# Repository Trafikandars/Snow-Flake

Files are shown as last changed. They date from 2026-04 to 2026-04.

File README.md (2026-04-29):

# Snow-Flake
Machine à Neige DMX pour le Theâtre - DMX Snow Flake Machine for theater

Ce projet vous est proposé par la compagnie Trafikandars :

C'est une machine permettant de lâcher des cotillons ou autre, contrôlable en DMX.
La construction nécessite des pièces imprimées en 3D et un circuit imprimé sur mesure. 
Tous les fichiers sont disponibles ici pour que vous puissiez la faire vous-même. 
Si vous n’avez pas le matériel nous vous proposons de vous envoyer un kit contenant tous les éléments nécessaire à son assemblage pour la monter ou de vous l’envoyer prête à l’usage.
Si vous trouvez des pistes d'améliorations je reste ouvert à toute requet : Trafikandars.workshop@gmail.com

Conception 3D : Adem Koanda_Saurel

Code : Côme Douville

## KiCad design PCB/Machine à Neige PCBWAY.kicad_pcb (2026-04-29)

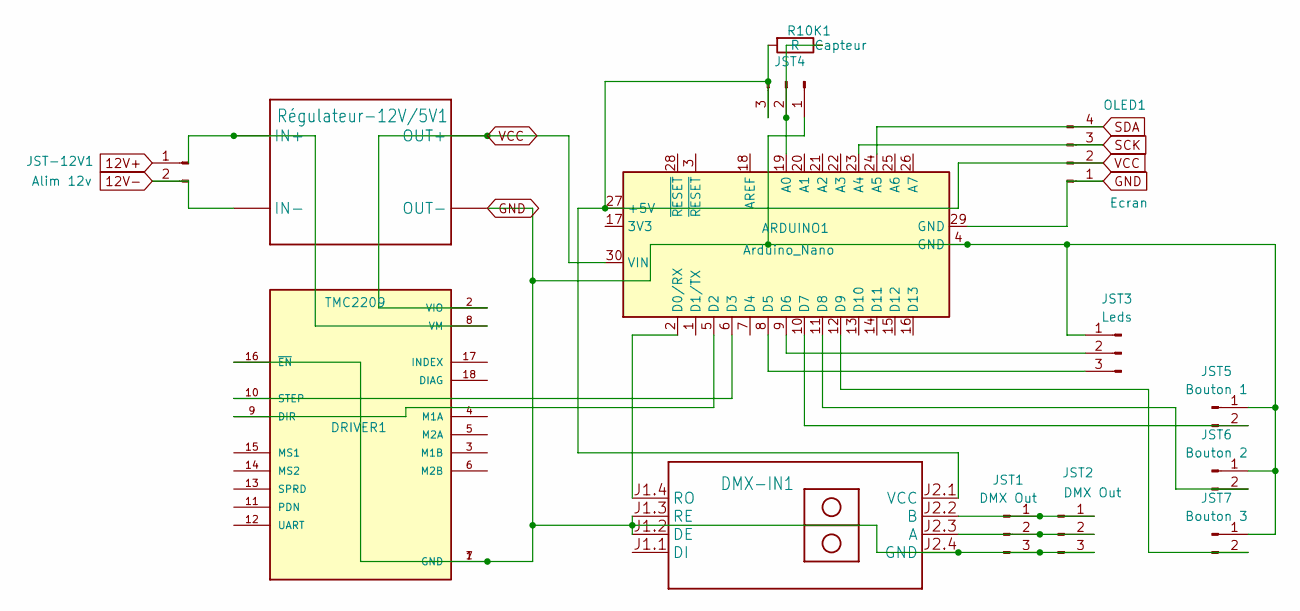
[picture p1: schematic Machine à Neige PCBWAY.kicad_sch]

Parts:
ARDUINO1: Arduino_Nano
DMX-IN1: RS485-TTL-CONVERTER
DRIVER1: TMC2209; MODULE_TMC2209_SILENTSTEPSTICK; PARTREV 1.20
JST1, JST2: DMX Out; PinSocket_1x03_P2.54mm_Vertical
JST3: Leds; PinSocket_1x03_P2.54mm_Vertical
JST4: Capteur; PinSocket_1x03_P2.54mm_Vertical
JST5: Bouton 1; PinSocket_1x02_P2.54mm_Vertical
JST6: Bouton 2; PinSocket_1x02_P2.54mm_Vertical
JST7: Bouton 3; PinSocket_1x02_P2.54mm_Vertical
JST-12V1: Alim 12v; PinSocket_1x02_P2.54mm_Vertical
OLED1: Ecran; PinSocket_1x04_P2.54mm_Vertical
R10K1: R; R_Axial_DIN0207_L6.3mm_D2.5mm_P5.08mm_Vertical
Régulateur-12V/5V1: StepDown-lm2596

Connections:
12V+: JST-12V1.1
12V-: JST-12V1.2, Régulateur-12V/5V1.2 (IN-)
GND: ARDUINO1.4 (GND), ARDUINO1.29 (GND), DMX-IN1.J1.2 (DE), DMX-IN1.J1.3 (RE), DMX-IN1.J2.4 (GND), DRIVER1.1 (GND), DRIVER1.7 (GND), DRIVER1.16 (~EN), JST1.3, JST2.3, JST3.1, JST4.1, JST5.1, JST6.1, JST7.1, OLED1.1, Régulateur-12V/5V1.4 (OUT-)
unnamed: ARDUINO1.19 (A0), JST4.2, R10K1.1
unnamed: ARDUINO1.2 (D0/RX), DMX-IN1.J1.4 (RO)
unnamed: ARDUINO1.5 (D2), DRIVER1.9 (DIR)
unnamed: ARDUINO1.6 (D3), DRIVER1.10 (STEP)
unnamed: ARDUINO1.8 (D5), JST3.3
unnamed: ARDUINO1.9 (D6), JST3.2
unnamed: ARDUINO1.10 (D7), JST5.2
unnamed: ARDUINO1.11 (D8), JST6.2
unnamed: ARDUINO1.12 (D9), JST7.2
unnamed: DMX-IN1.J2.3 (A), JST1.2, JST2.2
unnamed: DMX-IN1.J2.2 (B), JST1.1, JST2.1
unnamed: DRIVER1.8 (VM), Régulateur-12V/5V1.1 (IN+)
SCK: ARDUINO1.23 (A4), OLED1.3
SDA: ARDUINO1.24 (A5), OLED1.4
VCC: ARDUINO1.27 (+5V), ARDUINO1.30 (VIN), DMX-IN1.J2.1 (VCC), DRIVER1.2 (VIO), JST4.3, OLED1.2, R10K1.2, Régulateur-12V/5V1.3 (OUT+)

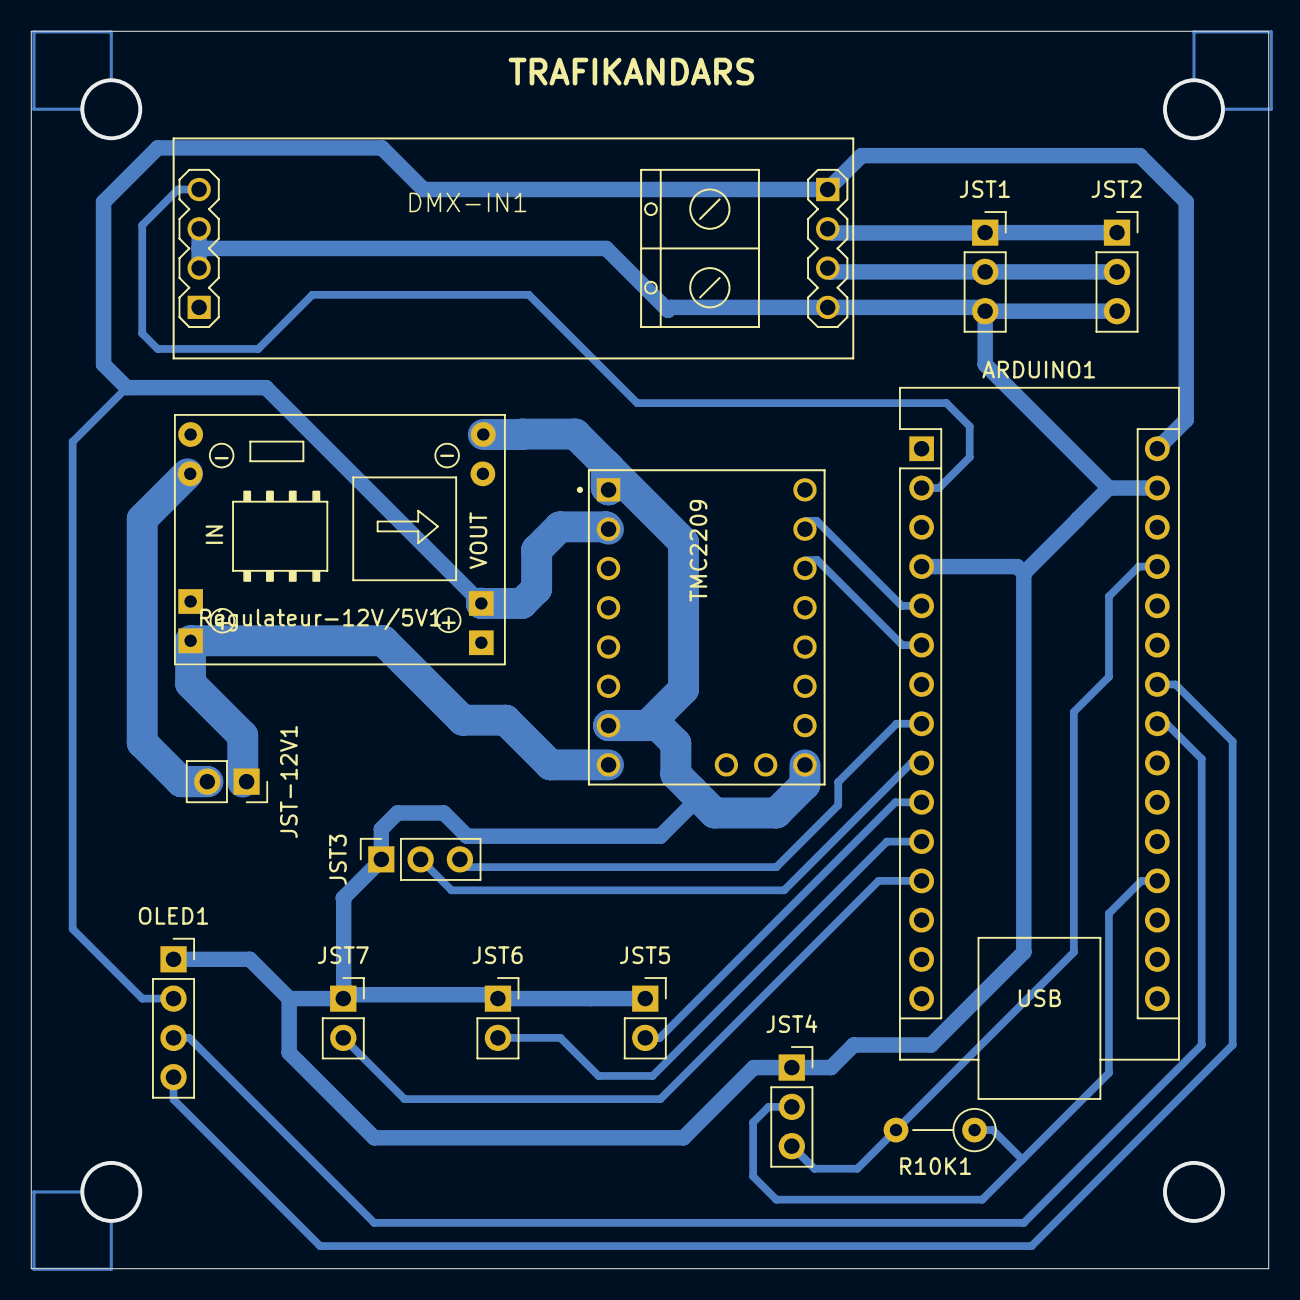
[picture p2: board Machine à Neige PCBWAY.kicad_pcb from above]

Board: 2 copper layers, 80.0 x 80.0 mm, 14 parts (0 on the bottom side), 17 nets.

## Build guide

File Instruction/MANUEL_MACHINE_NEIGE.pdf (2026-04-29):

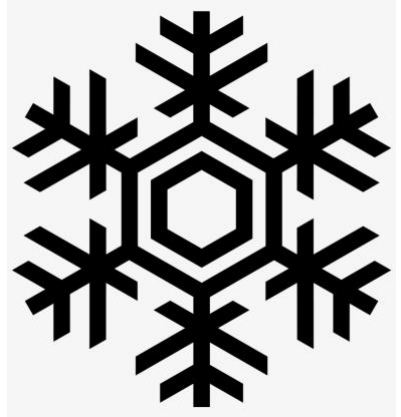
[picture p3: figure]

# Manuel D’utilisation

## Alimentation

12 V - 3A Minimum (CC)

## Mode de Fonctionnement

### Mode ROTATION :

Ce mode permet de faire tourner la machine sur elle-même de façon continue.
Il utilise 1 Canal DMX permettant de faire varier la vitesse de rotation. (Si ce canal est inférieur à 10%, la machine reste fixe.)

### Mode SHAKE :

Ce mode permet de faire des « aller-retour », tête en bas.
Il utilise 2 Canaux DMX :
Canal 1 : Vitesse (une vitesse minimal est imposé, donc même à 0 ce canal transmet une vitesse de rotation non nulle).
Canal 2 : Angle de Rotation de 0 à 180°. (Si ce canal est inférieur à 10%, la machine reste fixe.)

## Utilisation

A l’allumage la machine cherche à retrouver sa position HOME (Trous vers le Haut).

Cette position est regagnée lorsque la position fixe est demandée, ou que le signal DMX est perdu.

La machine se met sur le dernier mode sélectionné.

Il faut appuyer sur ENTER (bouton de couleur) pour pouvoir rentrer dans les paramètres.

On a alors accès à l’adressage DMX (Menu 1 ) et à la sélection du mode (Menu 2).

Le Menu CONFIGURATION (Menu 3) permet de fixer des limites plus faibles que le maximum autorisé permettant ainsi d’avoir une course de fader plus précise.

Le Menu RESTART (Menu 4) permet de redémarrer la machine une fois les changements effectués.

La machine possède 2 LEDS :

Rouge : POWER, la machine est sous tension.

Data : Vert la machine reçoit un signal DMX.

### Des essais sont nécessaires permettant de choisir le bon mode et les bonnes

valeurs et la bonne taille de trous (tous les cotillons étant différents).

### Réglage-Recharge

2 visses Permettent d’écarter la partie sans écran et ainsi d’enlever le tube. Celui-ci possède un capuchon, permettant de le remplir.

Une visse permet de sélectionner la taille des trous entre petits, moyens et gros, suivant l’effet voulu.

Attention :

Si une croix apparait sur le coin supérieur droit de l’écran, le capteur de position est défectueux. La machine ne trouvera pas le HOME (Trou vers le Haut).

Il faut débrancher la machine, aligner le capteur avec l’aimant (approximativement) et remettre la machine sous tension.

TO DO :

Si le problème persiste un mode DEBUG permet de vérifier son fonctionnement dans le menu CONFIGURATION : il permet de lire la valeur des variables écrites dans la mémoire interne, la valeur renvoyer par le capteur de position (l’aimant doit être en face) ainsi que la lecture des 2 canaux DMX lu par la machine.

Un mode dégradé est activable dans ce menu DEBUG. Il permet de faire fonctionner la machine si le capteur de position est H.S. : la machine prend alors comme point Zéro sa position à l’allumage, il faut donc vérifié que les trous soit vers le haut lors de la mise sous tension. Lors de l’utilisation, au lieu d’afficher le canal DMX et la valeur d’angle max ou de vitesse max, il est écrit CAPTEUR OFF.

En cas de problème priez.

(Fort)

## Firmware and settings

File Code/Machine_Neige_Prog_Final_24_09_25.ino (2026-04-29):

//Barre 12mm alu Tube PVC 100mm interieur 97

// Bitmap noir 8x8
const uint8_t blackBitmap8x8[] PROGMEM = {
  0xFF,  // Ligne 1 : 11111111
  0xFF,  // Ligne 2
  0xFF,  // Ligne 3
  0xFF,  // Ligne 4
  0xFF,  // Ligne 5
  0xFF,  // Ligne 6
  0xFF,  // Ligne 7
  0xFF   // Ligne 8
  };
const uint8_t blackBitmap24x8[] PROGMEM = {
  0xFF, 0xFF, 0xFF,  // Ligne 1 (24 pixels blancs)
  0xFF, 0xFF, 0xFF,  // Ligne 2
  0xFF, 0xFF, 0xFF,  // Ligne 3
  0xFF, 0xFF, 0xFF,  // Ligne 4
  0xFF, 0xFF, 0xFF,  // Ligne 5
  0xFF, 0xFF, 0xFF,  // Ligne 6
  0xFF, 0xFF, 0xFF,  // Ligne 7
  0xFF, 0xFF, 0xFF   // Ligne 8
  };

//___________________________________________
//
/**************  LIBRAIRIES   ***************/
//___________________________________________
#include <avr/wdt.h>   // pour le reset
//DMX
#include <DMXSerial.h>
#include <DMXSerial_avr.h>
#include <DMXSerial_megaavr.h>
//ECRAN
#include <SPI.h>
#include <Wire.h>
#include <Adafruit_GFX.h>
#include <Adafruit_SSD1306.h>
#define SCREEN_WIDTH 128
#define SCREEN_HEIGHT 32
#define OLED_RESET     -1 // Reset pin # (or -1 if sharing Arduino reset pin)
#define SCREEN_ADDRESS 0x3C //I2C Adresse
Adafruit_SSD1306 display(SCREEN_WIDTH, SCREEN_HEIGHT, &Wire, OLED_RESET);

//Moteur
#include <AccelStepper.h>
#include <MultiStepper.h>
#define DIR_PIN 6
#define STEP_PIN 5
AccelStepper stepper(AccelStepper::DRIVER, STEP_PIN, DIR_PIN);
//EEPROM
#include <EEPROM.h>

//___________________________________________
//
/**************  PIN PLANNER   ***************/
//___________________________________________


//Analog IN
#define CAPTEUR_HALL A0
#define BP_UP A3
#define BP_DOWN A2
#define BP_ENTER A1
//Digital OUT
#define LED_DATA 9
#define LED_POWER 8


//___________________________________________
//
/**************  VARIABLE   ***************/
//___________________________________________


bool Erreur = false ;

//DMX
int Channel_Dmx = 1 ;           //Adresse DMX
int Channel_1_Value = 0 ;       //Valeur de du Channel vitesse
int Channel_2_Value = 0 ;       // Angle
unsigned long lastPacket = 0;   //Temps depuis le dernier paquet DMX
bool No_Data = false ;
//Moteur
int Max_Speed = 650;
int Acceleration_Max = 3000;
int Acceleration = 500;
byte Direction_Moteur = 1;
bool Home = false ;
int Vitesse_Rotation = 0;
int Vitesse_To_Home = 50;
long Target = 100 ; 
int Angle_Max = 360 ;
int Target_Max = 0;
int Sens_Rot = -1;
int Angle = 0;
//Time
unsigned long Time1 = 0;
unsigned long Time2 = 0;
//Capteur
int Capteur = 0;
bool Etat_Capteur = 0;
//Mode
bool Mode = false;  //1 = Rotation ; 0 = SHAKE

//Clavier 
#define BP_none 0     //Retour d'infos de la fonction
#define Bp_Up 1
#define Bp_Down 2
#define Bp_Enter 3
int Key_Value = 0 ;
byte Key = 0 ;

//Ecran
int Curseur = 1;
int Page = 1 ;
bool Yes_No = false ;
unsigned long dernierAffichage = 0;
const unsigned long intervalAffichage = 1000; // en ms

//___________________________________________
//
/**************  FONCTIONS   ***************/
//___________________________________________

//---RESTART
void RESET(){
  wdt_enable(WDTO_15MS); // Active le watchdog avec un timeout de 15ms
  while(1); // Boucle infinie pour forcer le reset
  }

//---EEPROM
void Eeprom_reset(){
  Channel_Dmx = 1;
  Mode = false;
  Max_Speed = 600;
  Acceleration_Max = 3000;
  Vitesse_To_Home = 100 ;
  Angle_Max = 180 ;
  EEPROM.put(0,Channel_Dmx);
  EEPROM.put(4,Mode);
  EEPROM.put(8,Max_Speed);
  EEPROM.put(12, Acceleration_Max);
  EEPROM.put(16, Vitesse_To_Home);
  EEPROM.put(20,Angle_Max);
  }//END Eeprom_reset

void Eeprom_Read(){
  EEPROM.get(0,Channel_Dmx);
  EEPROM.get(4,Mode);
  EEPROM.get(8,Max_Speed);
  EEPROM.get(12, Acceleration_Max);
  EEPROM.get(16, Vitesse_To_Home);
  EEPROM.get(20,Angle_Max);
} //END Eeprom_get

//---DMX
void Dmx_Read(){
  Channel_1_Value = DMXSerial.read(Channel_Dmx);
  Channel_2_Value = DMXSerial.read(Channel_Dmx+1);
  }

//---Lecture Analog
void Read_bouton(){
  Key_Value = 0;
  if(analogRead(BP_UP)<800){
    Key_Value = Bp_Up;
    }
  if(analogRead(BP_DOWN)<800){
    Key_Value = Bp_Down;
    }
  if(analogRead(BP_ENTER)<800){
    Key_Value = Bp_Enter;
    }
  } //END Read_Bouton()

void Read_Bp_Enter_Only(){
  Key_Value = 0;
  if(analogRead(BP_ENTER)>800){
    Key_Value = Bp_Enter;
    }
  }//END Read Enter

void Read_capteur(){
 if (analogRead(A0)<500) Etat_Capteur = true;
 else Etat_Capteur = false ;
 }

void Angle_To_Target(){
    Target_Max = (Angle_Max/1.8);
    //Target = map(Angle, 0, Angle_Max, 0, Target_Max);
    }


//---Move
void First_Home(){
  int FirstHome = 25 ;
  int Speed_First_Home = 80;
  Read_capteur();
  stepper.setSpeed(50);
  display.clearDisplay();
  display.drawLine(0,0,128,0,SSD1306_WHITE);
  display.setCursor(30, 8); display.print(F("HOME LOOSE"));
  display.setCursor(56, 18); display.print(F("!"));
  display.drawLine(0,31,128,31,SSD1306_WHITE);
  display.display();
  Read_capteur();
  stepper.setSpeed(Speed_First_Home);
     while (!Etat_Capteur) {
      Read_capteur();
      stepper.moveTo(FirstHome);
      stepper.runSpeedToPosition();
      if (stepper.distanceToGo() == 0){
          FirstHome *= -2 ;  
          }
    Time2 = millis();    
    if ((Time2-Time1)>15000) {
      Etat_Capteur = true;
      Erreur = true ;
      Key_Value = 0;
      while(Key_Value != Bp_Enter){
        Read_bouton();
        display.clearDisplay();
        display.drawLine(0,0,128,0,SSD1306_WHITE);
        display.setCursor(30, 8); display.print(F("ERROR SENSOR"));
        display.setCursor(56, 18); display.print(F("!"));
        display.drawLine(0,31,128,31,SSD1306_WHITE);
        display.display();
        }  
        //SENSOR_DISPLAY();
        }
    }//while

  }  // HOME TROUVE

void Goto_Home(){
/*  display.drawBitmap(120, 0, blackBitmap8x8, 8, 8, SSD1306_BLACK);
  display.setCursor(120, 0); display.print(F("H"));
  display.display();  */
  Home = 0;
  stepper.setSpeed(Vitesse_To_Home);
  while (!Home){
    if (analogRead(CAPTEUR_HALL)<200) Home = true ;
    else Home = false ;
    stepper.setSpeed(Vitesse_To_Home);
    stepper.runSpeed();
    }//while !Home
    Home = 0;
    delay(80);
    //si trop rapide et dépasse
    while (!Home){
      if (analogRead(CAPTEUR_HALL)<200) Home = true ;
      else Home = false ;
      stepper.setSpeed(-Vitesse_To_Home);
      stepper.runSpeed();
      }//while !Home
      Home = 0;
      stepper.setCurrentPosition(0);
  }// END HOME

//___________________________________________
//
/**************   MODE  ***************/
//___________________________________________

//----------------------------
//---    MODE ROTATION    ----
//----------------------------
void Display_Rotation(){
  display.clearDisplay();
  display.setCursor(25, 0); display.print(F("MODE Rotation"));
  display.drawLine(0,8,128,8,SSD1306_WHITE);//Ligne en dessous
  display.setCursor(0, 11); display.print(F("DMX Add.  : ")); display.setCursor(95, 11);display.print(Channel_Dmx);
  display.setCursor(0, 20); display.print(F("Max Speed : ")); display.setCursor(95, 20);display.print(Max_Speed);
  display.display();
  }

void Mode_Rotation(){
  Display_Rotation();
  Vitesse_Rotation = 0;
  Key_Value = 0;
  while(Key_Value == 0){
    Display_Whilerunning();    
    Read_Bp_Enter_Only(); Key_Value = 0;
    Channel_1_Value = DMXSerial.read(Channel_Dmx);
    if (Channel_1_Value < 25) {
        Channel_1_Value = 0;
        Goto_Home();
        Channel_1_Value = DMXSerial.read(Channel_Dmx);
        while (Channel_1_Value < 25){
              Channel_1_Value = DMXSerial.read(Channel_Dmx);
              Display_Whilerunning();
                  if(analogRead(BP_ENTER)>800){
                    Menu_Start();
                    }
              }
        }
    Vitesse_Rotation = map(Channel_1_Value,0,255,0,Max_Speed);
    stepper.setSpeed(Vitesse_Rotation);
    stepper.runSpeed();
    }
  Goto_Home();
  delay(150);
  Key_Value = 0;
  Menu_Start();
  }//END Mode Rotation

//----------------------------
//---     MODE SHAKE      ----
//----------------------------
void Display_Shake(){
  Angle_To_Target();
  display.clearDisplay();
  display.setCursor(25, 0); display.print(F("MODE SHAKE"));
  display.drawLine(0,8,128,8,SSD1306_WHITE);//Ligne en dessous
  display.setCursor(0, 11); display.print(F("DMX Add.  : ")); display.setCursor(95, 11);display.print(Channel_Dmx);
  display.setCursor(0, 20); display.print(F("Angle Max : "));display.setCursor(95, 20); display.print(Angle_Max);
  display.drawBitmap(120, 0, blackBitmap8x8, 8, 8, SSD1306_BLACK);
  display.display();
  }

void Mode_Shake(){
  Display_Shake();
  Angle_To_Target(); //definit traget_max en fonction de l'angle max
  stepper.setAcceleration(Acceleration); 
  Sens_Rot = -1;
  Key_Value = 0;
  Dmx_Read(); 
  while(Key_Value == 0){
    Read_Bp_Enter_Only();
    Display_Whilerunning();
    Dmx_Read();  
    if (Channel_1_Value < 25){
        Channel_1_Value = 0;
        Goto_Home();
        Channel_1_Value = DMXSerial.read(Channel_Dmx);
        while (Channel_1_Value < 25){
          Channel_1_Value = DMXSerial.read(Channel_Dmx);
          //Display_Whilerunning();
          if(analogRead(BP_ENTER)>800){
              Menu_Start();
              }
        }
    }// if < 25
    Acceleration = map(Channel_2_Value,0,255,20, Acceleration_Max);
    Target = map(Channel_1_Value,0,255, 0, Target_Max) * Sens_Rot;
    stepper.setAcceleration(Acceleration);       //stepper.setAcceleration(Vitesse_Rotation);
    stepper.moveTo(100 + Target);                   //stepper.moveTo(Target);
    stepper.run();
    if (stepper.distanceToGo() == 0){
      Sens_Rot = -Sens_Rot;
      }
    }//while ENTER
  Goto_Home();
  delay(150);
  Key_Value = 0;
  Menu_Start();
  }//END Mode Shake

//___________________________________________
//
/**************   DISPLAY  ***************/
//___________________________________________


 void Display_Whilerunning(){   //   FUCKING SHIIT
   Display_Data();
   if (No_Data){
      Goto_Home();
      /*stepper.setAcceleration(500);
      stepper.moveTo(0);
      stepper.runToPosition();*/
      Key_Value = 0;
      while(DMXSerial.noDataSince() > 2000) {
          Read_Bp_Enter_Only();
          display.clearDisplay();
          display.drawLine(0,0,128,0,SSD1306_WHITE);//Ligne en dessous
          display.setCursor(40, 11); display.print(F("DATA LOST"));
          display.drawLine(0,31,128,31,SSD1306_WHITE);//Ligne en dessous
          display.display();
          if (Key_Value == Bp_Enter){
          Menu_Start();
          }
         }
        if(Mode == 1) Display_Rotation();
        if(Mode == 0) Display_Shake(); 
      }
   if ((millis() - Time1) > 2000) {
    //display.display(); // lent → on le fait rarement
    Time1 = millis();
    }
   }

void Display_Data(){
 if (DMXSerial.noDataSince() < 2000) {
    digitalWrite(LED_DATA, HIGH);
    No_Data = false;
    }
  else {
    digitalWrite(LED_DATA, LOW);
    No_Data = true;
 //   stepper.setSpeed(0);
 //   stepper.setAcceleration(0);
    }   
   }

void Display_Cursor(){
    if ((Curseur%2) == 1){
      display.setCursor(120, 11);display.print(F(">"));
      }
    if ((Curseur%2) == 0 ){
      display.setCursor(120, 20);display.print(F(">"));
      }
    }//END Display_Cursor

void Cursor_Move(int Cursor_Max){
    if (Key_Value == Bp_Up){ 
      Curseur += 1;
      if (Curseur > Cursor_Max) Curseur = 1 ;
      }
    if (Key_Value == Bp_Down){ 
      Curseur -= 1; 
      if (Curseur < 1) Curseur = Cursor_Max ; 
      }
   if ((Curseur == 1) || (Curseur == 2)) {
      Page = 1;
      }
   if ((Curseur == 3) || (Curseur == 4)) {
      Page = 2;
      }
  if ((Curseur == 5) || (Curseur == 6)) {
      Page = 3;
      }
  if ((Curseur == 7) || (Curseur == 8)) {
      Page = 4;
      }
  delay(200);
  }

int Valeur_Selection (int Val_Min, int Val_Max, int Increment, int Valeur_To_Set){
      display.setCursor(0, 20); 
      display.print(F("<"));display.setCursor(120, 20); display.print(F(">"));
      display.setCursor(60, 20); display.print(Valeur_To_Set);
      if (Key_Value == Bp_Up){ 
        Valeur_To_Set += Increment; 
        if (Valeur_To_Set >Val_Max) Valeur_To_Set = Val_Min ;
        }
      if (Key_Value == Bp_Down){ 
        Valeur_To_Set -= Increment;
        if (Valeur_To_Set <Val_Min) Valeur_To_Set = Val_Max ;
        }
 return Valeur_To_Set ;        
 } //Valeur Selection


//___________________________________________
//
/**************  Menu   ***************/
//___________________________________________

void Menu_Adresse(){
  Key_Value = 0;
  while(Key_Value != Bp_Enter){
      Read_bouton();
      display.clearDisplay();
      display.setCursor(25, 0); display.print(F("ADRESSE DMX"));
      display.drawLine(0,8,128,8,SSD1306_WHITE);//Ligne en dessous
      display.setCursor(0, 20); display.print(F("<"));display.setCursor(120, 20); display.print(F(">"));
      display.setCursor(55, 20); display.print(Channel_Dmx);
      if (Key_Value == Bp_Up){ 
        Channel_Dmx += 1; 
        if (Channel_Dmx >512) Channel_Dmx = 1 ;
        }
      if (Key_Value == Bp_Down){ 
        Channel_Dmx -= 1;
        if (Channel_Dmx <1) Channel_Dmx = 512 ;
        }  
      display.display();
      delay(80);
  }//while 1
  EEPROM.put(0, Channel_Dmx );
  delay(100);
  }//END ADRESSE DMX

void Menu_Mode(){
  Key_Value = 0;
  while(Key_Value != Bp_Enter){
      Read_bouton();
      display.clearDisplay();
      display.setCursor(50, 0); display.print(F("MODE"));
      display.drawLine(0,8,128,8,SSD1306_WHITE);//Ligne en dessous
      display.setCursor(0, 20); display.print(F("<"));display.setCursor(120, 20); display.print(F(">"));
      if (Mode) {
          display.setCursor(40, 20); 
          display.print(F("Rotation"));
          }
      if (!Mode) {
         display.setCursor(45, 20); 
         display.print(F("SHAKE"));
         }
      if (Key_Value == Bp_Up){ 
        Mode = !Mode; 
        }
      if (Key_Value == Bp_Down){ 
        Mode = !Mode;
        }  
  display.display();
  delay(150);
  }//while ENTER
  EEPROM.put(4, Mode);
  delay(50);
  RESET();
  }

void Menu_Config(){
  delay(180);
  Curseur = 1 ;
  Page = 1 ;
  Key_Value = 0;
  while(Key_Value != Bp_Enter){
  display.clearDisplay();
  display.setCursor(25, 0); display.print(F("CONFIGURATION")); 
  display.drawLine(0,8,128,8,SSD1306_WHITE);
    Read_bouton();
    Cursor_Move(7);
    Display_Cursor(); //Position Selection Ligne
    if (Page == 1){
      display.setCursor(0, 11); display.print(F("1-Speed Mode ROT."));
      display.setCursor(0, 20); display.print(F("2-Speed Mode SHAKE"));
      }
  if (Page == 2){
    display.setCursor(0, 11); display.print(F("3-Angle Mode SHAKE"));
    display.setCursor(0, 20); display.print(F("4-Speed Homing"));
    }  
    if (Page == 3){
    display.setCursor(0, 11); display.print(F("5-EEPROM RESET"));
    display.setCursor(0, 20); display.print(F("6-DEBUG"));
    } 
  if (Page == 4){
    display.setCursor(0, 11); display.print(F("7-BACK"));
    display.setCursor(0, 20); display.print(F(""));
    } 

  display.display();
  }
 if (Curseur == 1) {
    Key_Value = 0;
    while(Key_Value != Bp_Enter){
      Read_bouton();
      display.clearDisplay();
      display.setCursor(15, 0); display.print(F("Max Speed ROT.")); 
      display.drawLine(0,8,128,8,SSD1306_WHITE);
      Max_Speed = Valeur_Selection (100, 600, 100, Max_Speed);
      display.display();
      delay(150);
      }//while Enter
  EEPROM.put(8,Max_Speed);
 }
 if (Curseur == 2) {
    Key_Value = 0;
    while(Key_Value != Bp_Enter){
      Read_bouton();
      display.clearDisplay();
      display.setCursor(18, 0); display.print(F("Max Speed SHAKE")); 
      display.drawLine(0,8,128,8,SSD1306_WHITE);
      Acceleration_Max = Valeur_Selection (1000, 4000, 1000, Acceleration_Max); //min, max, incrent, variable
      display.display();
      delay(150);
      }//while Enter
    EEPROM.put(12, Acceleration_Max);
    }
 if (Curseur == 3) {
    Key_Value = 0;
    while(Key_Value != Bp_Enter){
      Read_bouton();
      display.clearDisplay();
      display.setCursor(25, 0); display.print(F("Angle Max")); 
      display.drawLine(0,8,128,8,SSD1306_WHITE);
      Angle_Max = Valeur_Selection(10, 360, 10, Angle_Max); //min, max, incrent, variable
      display.display();
      delay(150);
      }//while Enter
    EEPROM.put(20,Angle_Max);
    }
 if (Curseur == 4) {
    Key_Value = 0;
    while(Key_Value != Bp_Enter){
      Read_bouton();
      display.clearDisplay();
      display.setCursor(25, 0); display.print(F("Vitesse Homing")); 
      display.drawLine(0,8,128,8,SSD1306_WHITE);
      Vitesse_To_Home = Valeur_Selection (100, 1000, 100, Vitesse_To_Home); //min, max, incrent, variable
      display.display();
      delay(150);
      }//while Enter
    EEPROM.put(16, Vitesse_To_Home);
    }
if (Curseur == 5) {
    Key_Value = 0;
    while(Key_Value != Bp_Enter){
      Read_bouton();
      display.clearDisplay();
      display.setCursor(25, 0); display.print(F("EEPROM RESET")); 
      display.drawLine(0,8,128,8,SSD1306_WHITE);
      display.setCursor(0, 20); display.print(F("<"));display.setCursor(120, 20); display.print(F(">"));
      if (Key_Value == Bp_Up) Yes_No = !Yes_No;
      if (Key_Value == Bp_Down) Yes_No = !Yes_No;
      display.setCursor(50, 20);
      if (Yes_No) display.print(F("YES"));
      if (!Yes_No) display.print(F("NO"));
      display.display();
      delay(150);
      }//while Enter
      if (Yes_No) Eeprom_reset();
      Menu_Config();
      }
      if (Curseur == 6) {
         Menu_Debug();
         }
      if (Curseur == 7) {
        Menu_Start();
        }
        
}//END CONFIGURATION


void Menu_Start(){
  delay(150);
  Curseur = 1 ;
  Page = 1 ;
  while(1){
  display.clearDisplay();
  Display_Data();
  display.setCursor(50, 0); display.print(F("MENU")); 
  display.drawLine(0,8,128,8,SSD1306_WHITE);
  if (Page == 1){
      display.setCursor(0, 11); display.print(F("1-DMX Add: ")); display.print(Channel_Dmx);
      display.setCursor(0, 20); display.print(F("2-Mode   : "));
      if(Mode == 1) display.println(F("Rotation"));
      if(Mode == 0) display.println(F("Shake")); 
      }
  if (Page == 2){
    display.setCursor(0, 11); display.print(F("3-Menu Config"));
    display.setCursor(0, 20); display.print(F("4-RESTART")); 
    }
    Read_bouton();
    if (Key_Value == Bp_Up){ 
      Curseur += 1;
      if (Curseur > 4) Curseur = 1 ;
      }
    if (Key_Value == Bp_Down){ 
      Curseur -= 1; 
      if (Curseur < 1) Curseur = 4 ; 
      }
   if ((Curseur == 1) || (Curseur == 2)) {
      Page = 1;
      }
   if ((Curseur == 3) || (Curseur == 4)) {
      Page = 2;
      }
    Display_Cursor(); //Position Selection Ligne
    display.display();
    delay(150);
    if (Key_Value == Bp_Enter){  
       if (Curseur == 1) Menu_Adresse();
       if (Curseur == 2) Menu_Mode(); 
       if (Curseur == 3) Menu_Config();
       if (Curseur == 4) Menu_RESET(); 
       }
    }//while 1
  }//END Menu_Start()

void Menu_RESET(){
 Key_Value = 0;
  while(Key_Value != Bp_Enter){
      Read_bouton();
      display.clearDisplay();
      display.setCursor(40, 0); display.print(F("RESTART"));
      display.drawLine(0,8,128,8,SSD1306_WHITE);
      display.setCursor(0, 20); display.print(F("<"));display.setCursor(120, 20); display.print(F(">"));
      if (Key_Value == Bp_Up) Yes_No = !Yes_No;
      if (Key_Value == Bp_Down) Yes_No = !Yes_No;
      display.setCursor(55, 20);
      if (Yes_No) display.print(F("YES"));
      if (!Yes_No) display.print(F("NO"));
      display.display();
      delay(150);
      }//while Enter
      if (Yes_No) RESET();
      else Menu_Start();
    }
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
void loop() {
 Menu_Start();
 //Menu_Config();
 //Mode_Rotation();
 //Mode_Shake();
/************************************************************************************/
/************************************************************************************/
//                               TEST
/************************************************************************************/
/************************************************************************************/

// >>>        AFFICHAGE ANALOG 
/*
   display.clearDisplay();
   display.setCursor(0, 0); display.print(analogRead(A1));
   delay(100);
   display.display();
*/
//  >>>      RUN SPEED

 //stepper.runSpeed();

 }// END LOOP



 /*   Dmx_Read();
    display.clearDisplay();
    display.setCursor(0, 0); display.print(DMXSerial.noDataSince());
    display.display();
    delay(100);
*/


/* Vitesse_Rotation = 2000;
 Target = 200;
 while (1){
        stepper.setAcceleration(Vitesse_Rotation);//stepper.setAcceleration(Vitesse_Rotation);
        stepper.moveTo(Target);//stepper.moveTo(Target);
        stepper.run();
        }

*/
/*
const uint8_t whiteBitmap24x8[] PROGMEM = {
  0xFF, 0xFF, 0xFF,  // Ligne 1 (24 pixels blancs)
  0xFF, 0xFF, 0xFF,  // Ligne 2
  0xFF, 0xFF, 0xFF,  // Ligne 3
  0xFF, 0xFF, 0xFF,  // Ligne 4
  0xFF, 0xFF, 0xFF,  // Ligne 5
  0xFF, 0xFF, 0xFF,  // Ligne 6
  0xFF, 0xFF, 0xFF,  // Ligne 7
  0xFF, 0xFF, 0xFF   // Ligne 8
};

  /*  
    stepper.setAcceleration(200);//stepper.setAcceleration(Vitesse_Rotation);
    stepper.moveTo(Target);//stepper.moveTo(Target);
    if (stepper.distanceToGo() == 0){
        Target = -Target;
        }
    stepper.run();*/
   



/*
    display.drawBitmap(120, 0, blackBitmap8x8, 8, 8, SSD1306_BLACK);
    display.setCursor(120, 0); display.print("R");
    display.setCursor(0, 0); display.print(lastPacket);
    display.display();
    delay(3000);
    display.drawBitmap(120, 0, blackBitmap8x8, 8, 8, SSD1306_BLACK);
    display.setCursor(120, 0); display.print("Q");
    display.display();
    delay(3000);
*/
    
//Va a la position : blocant le temps d'arriver
 /* stepper.setCurrentPosition(0);
  stepper.setAcceleration(1000);
  stepper.moveTo(200);//stepper.moveTo(Target);
  stepper.runToPosition();*/

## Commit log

2026-04-29 Create Arduino_Code
2026-04-29 Create PCB
